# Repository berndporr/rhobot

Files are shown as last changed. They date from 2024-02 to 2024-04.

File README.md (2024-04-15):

# RhoBot: A Robotics and AI platform

RhoBot is a mobile robot for research in obstacle avoidance built using an NVIDIA Jetson Nano, a Slamtec A1M8 RPLiDAR, a Raspberry Pi Cam v2, and two Parallax CR serco motors. The API provided in this repo provides an abstracted way to interface with the motors, however does not currently support interface with the LiDAR or camera so these would need to be implemented by a user.

<p align=center>
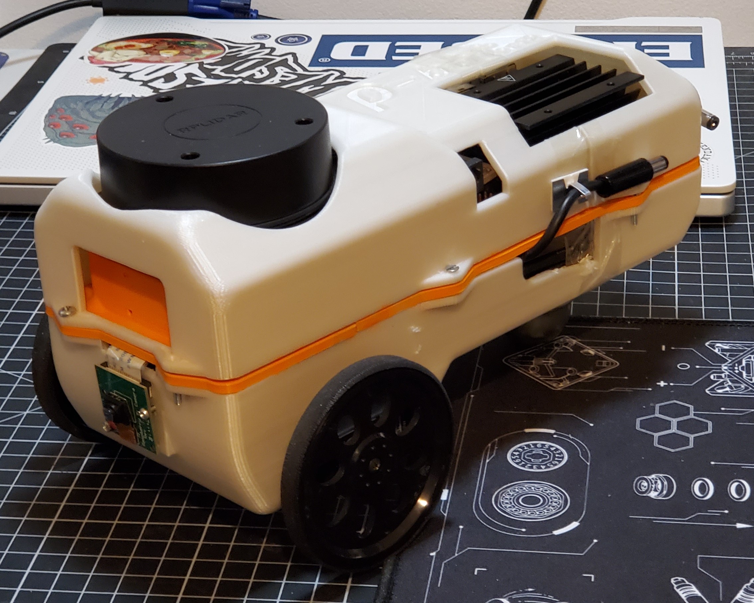
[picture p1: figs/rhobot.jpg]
Rhobot

</p>

## Table of contents

- Bill of Sale
- Enclosure and PCB Manufacture
- Build Guide and Set Up
- API Installation
- Sample Programs
- Credits

## Bill of Sale

| Part | Quantity | Cost (VAT included) | Where to buy |
| --- | --- | --- | --- |
| NVIDIA Jetson Nano | x1 | £167.94 | [RS Components](https://uk.rs-online.com/web/p/processor-development-tools/1999831?gb=s) |
| Parallax CR Servo Motor | x2 | £40.00 | [RS Components](https://uk.rs-online.com/web/p/servo-motors/7813046?gb=s) |
| Parallax Wheels | x2 | £6.40 | [Parallax](https://www.parallax.com/product/robot-wheel-molded-tire-for-servos/) |
| Ansmann Power Supply | x1 | £31.51 | [RS Components](https://uk.rs-online.com/web/p/power-banks/2498449?gb=s) |
| USB-A to DC Jack Cable | x2 | £12.84 | [RS Components](https://uk.rs-online.com/web/p/usb-cables/1862796?gb=s) |
| A1M8 LiDAR | x1 | £83.60 | [RobotShop](https://uk.robotshop.com/products/rplidar-a1m8-360-degree-laser-scanner-development-kit) |
| Raspberry Pi Camera v2 | x2 | £18.61 | [RS Components](https://uk.rs-online.com/web/p/raspberry-pi-cameras/9132664?gb=s) |
| USB Wifi Adapter | x1 | £12.00 | [RS Components](https://uk.rs-online.com/web/p/wifi-adapters/2558455?gb=s) |
| Total | ------- | £372.90 | ------- |

Necessary screws, nuts and bolts are not included in the bill of sale.

## Enclosure and PCB Manufacture

The enclosure is a three teir design and is fully 3D printable. In the CAD directory the their teirs are available in full and split to allow for printing on a smaller printer. The total print time is between 28 - 37 hours depending on material, and around £9 of filament. The weight is 0.3 kg.

If access to a 3D printer is not possible, the service [CraftCloud](craftcloud3d.com) have quoted £23.38 for the manufacture of the enclosure in PLA plastic.

The design files for the PCB were made using KiCAD and are available in the PCB directory. The service [PCBWay](pcbway.com) has quoted £4.01 for the manufacture of 10 boards.

## Build Guide and Set up

### Solder PCB
Firstly, sockets should be soldered onto the custom PCB. The 40 pin socket should be soldered to the bottom of the board and the remaining sockets should be mounted to the top of the board.

<p align=center>
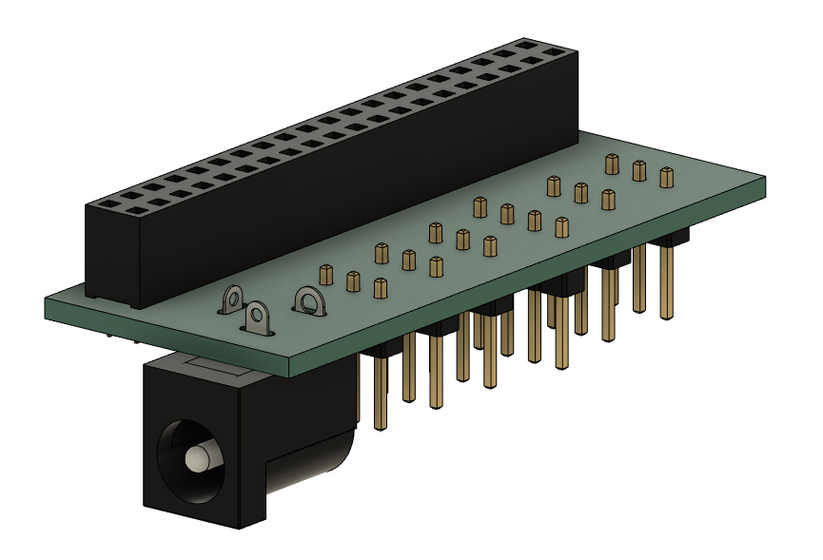
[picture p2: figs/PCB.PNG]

</p>

### Lowest Level
1) Screw the wheels onto the motors.
2) Use nuts and bolts to attach both motors to the "lower" enclosure component in the four mounting holes. Ensure the cables of the motors point towards the front of the enclosure so they will line up with the center of the LiDAR.
3) Use bolts screws to attach the camera to the mount on the "lower" component and route it's cable to the back of the enclosure.
4) Rest the power supply on top of the motors with the ports facing the back of the enclosure. Connect the USB-A to DC cables to the USB ports of the supply.

<p align=center>
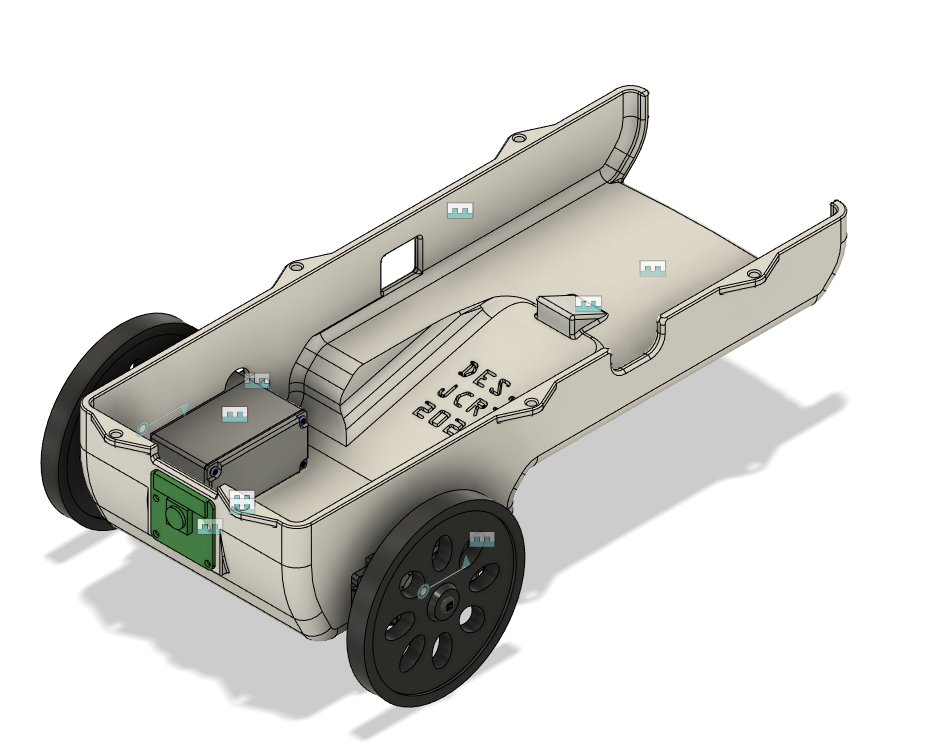
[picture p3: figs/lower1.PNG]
Lower A
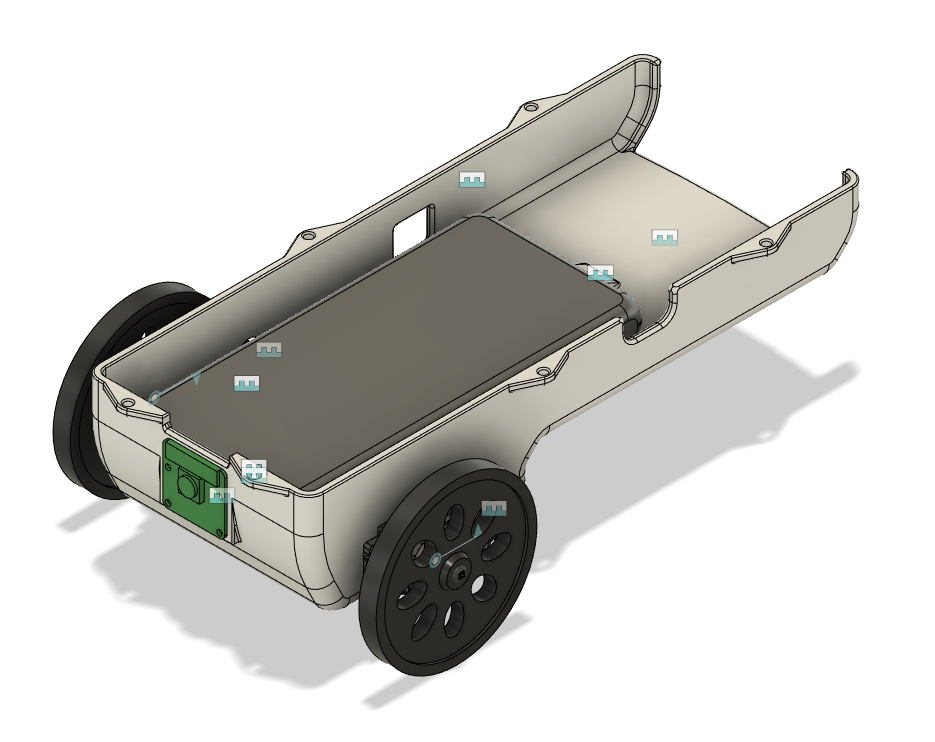
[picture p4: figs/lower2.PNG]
Lower B
 
</p>

### Middle Level
1) Use bolts to secure the Jetson to the lower standoffs of the "middle" enclosure component.
2) Use boolts to secure the LiDAR sensor to the higher standoffs of the "middle" component.
3) Attach the PCB to the 40 pin GPIO header of the Jetson.
4) Route the motors and camera wire through the slots in the "middle" component. Attach the camera cable to the CSI port of the Jetson. Attach the motors to the PCB using the relevant sockets, noting the circuit schematic.
5) Connect the LiDAR UART and motor cables to the PCB noting the schematic.
6) Place the "middle" component over the "lower" component.

<p align=center>
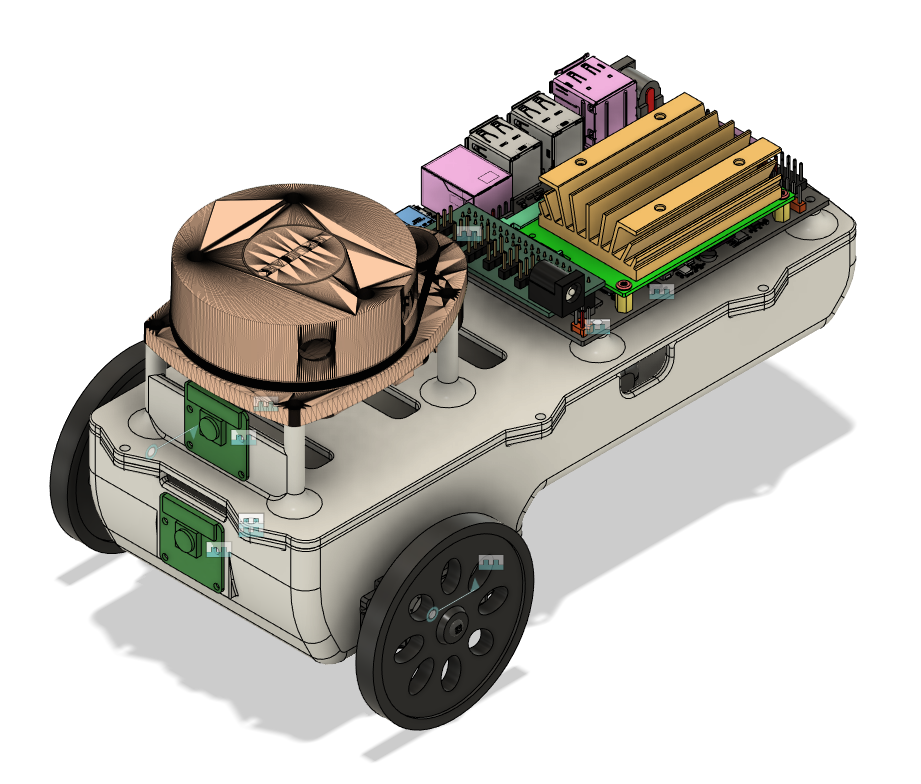
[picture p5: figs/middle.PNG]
Middle

</p>

### Upper Level
1) Place the "upper" component onto the "middle" componet and secure the enclosure with the sixe bolt holes around the perimeter.
2) Attach the USB Wifi adapter to a USB port on the Jetson
3) Connect the power supply to the Jetson and PCB through using the USB to DC cables.

<p align=center>
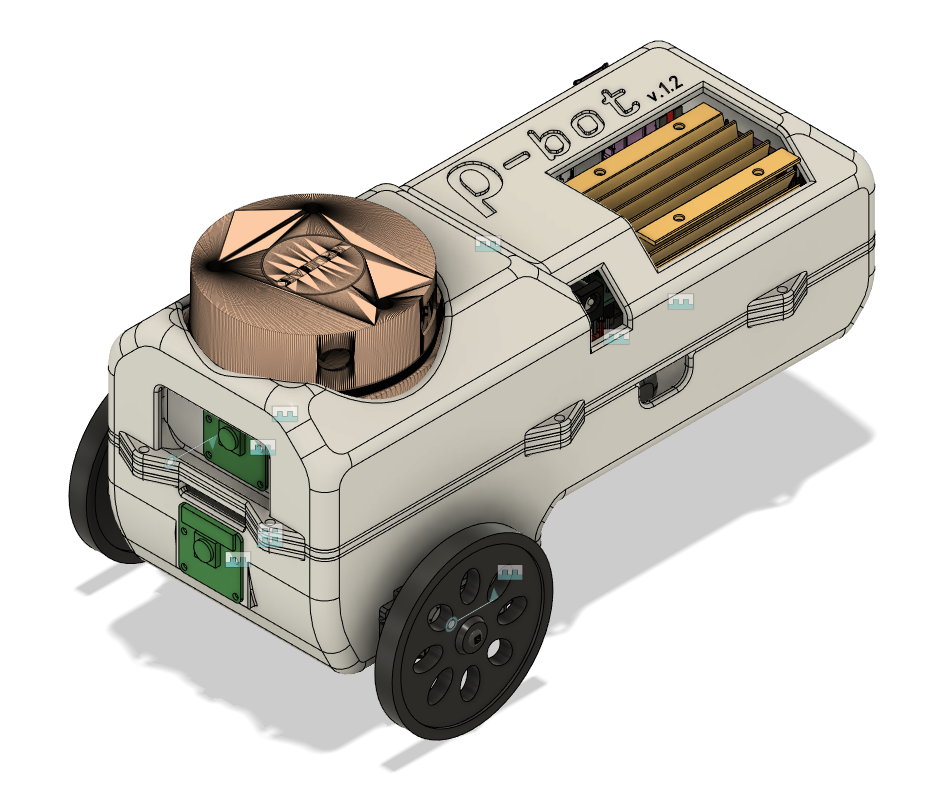
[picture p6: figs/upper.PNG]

</p>

### Jetson Set Up
For detailed instructions how how to set up the Jetson, click this [link](https://developer.nvidia.com/embedded/learn/get-started-jetson-nano-devkit).

Once the Jetson boots, connect to a wireless network using the Linux network manager.

## API Installation

### Dependencies
Clone and build the [JetsonGPIO](https://github.com/pjueon/JetsonGPIO) repository. This will install the library used to interface with the Jetson's GPIO header.

For the camer and LiDAR, the [jetson-inference]()https://github.com/dusty-nv/jetson-inference and [rplidar-sdk](https://github.com/Slamtec/rplidar_sdk) are recommended respectively.

### Build Project
Clone this repository and run the following commands to build the project:

`mkdir build && cd build`

`cmake ..`

`make`

This will build the API library and compile the sample programs.

## Sample Programs

sample programs are provided to test the motor interface. To execute them run the relevant of the following commands while in the build directory:

`./test_motors`

`./test_differential_steering`

`./test_lidar`

## Credits

This project has been supervised by Dr. Bernd Porr and is a continuation of work done on the [AlphaBot](https://github.com/berndporr/alphabot) and [SigmaBot](https://github.com/berndporr/sigmabot) projects.

RhoBot is ©️ copyright 2024 of J.C. Redmond III and any use of the material in this repository should be appropriately credited.

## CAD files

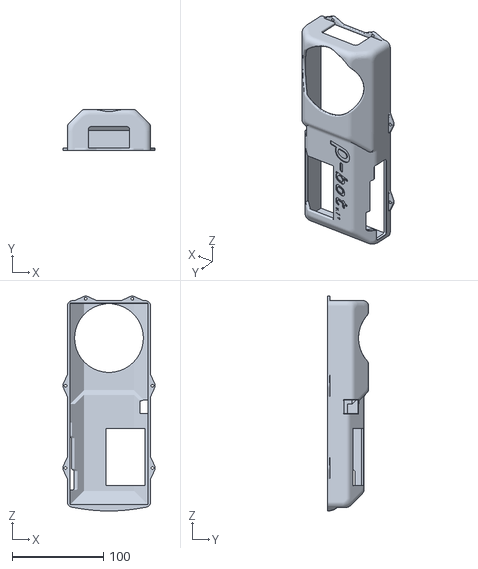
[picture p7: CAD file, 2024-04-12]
CAD/upper_full.stl
101.0 x 45.0 x 235.0

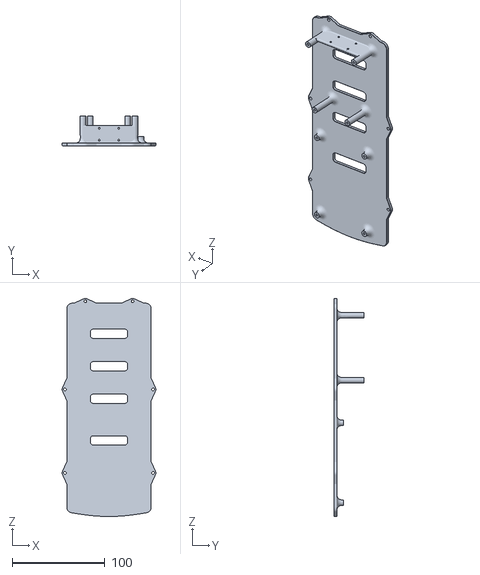
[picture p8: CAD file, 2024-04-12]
CAD/middle_full.stl
101.0 x 32.0 x 235.0

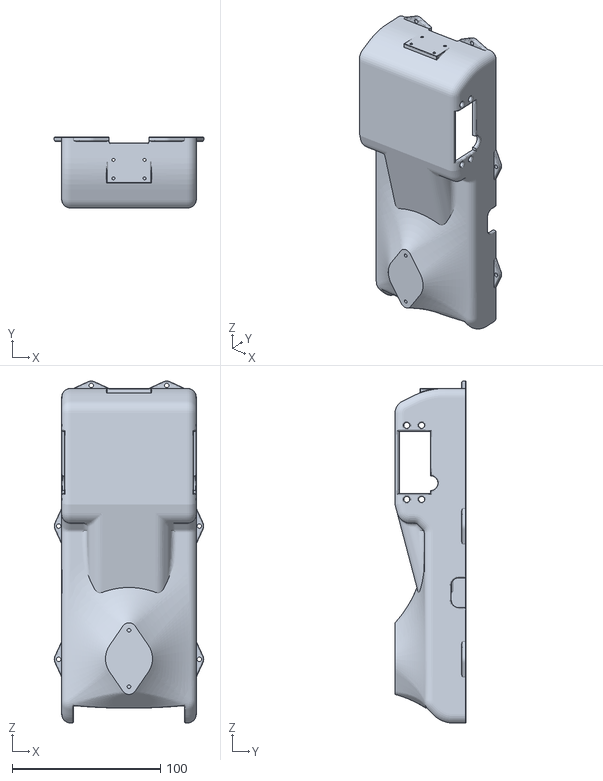
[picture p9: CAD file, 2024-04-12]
CAD/lower_full.stl
101.0 x 48.0 x 231.0

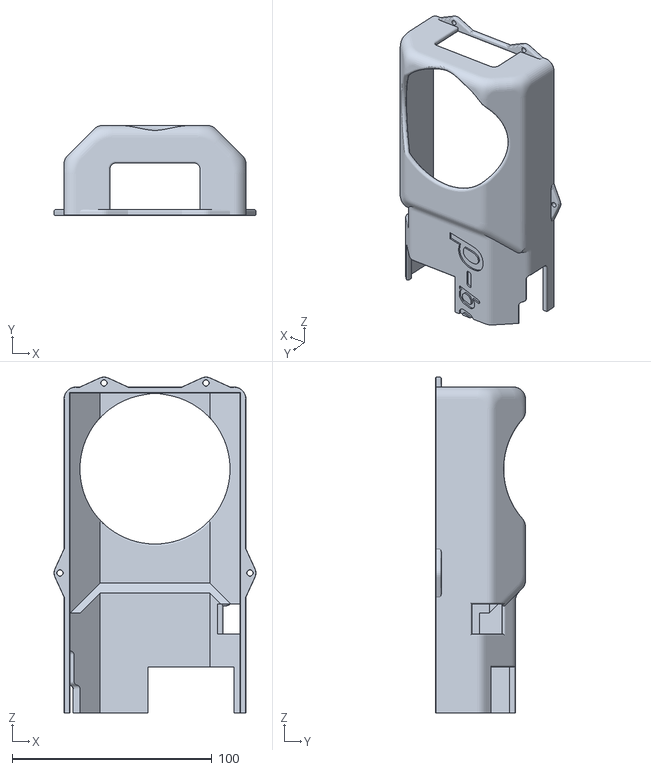
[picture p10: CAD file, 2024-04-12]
CAD/split components/upper_A.stl
101.0 x 45.0 x 168.0

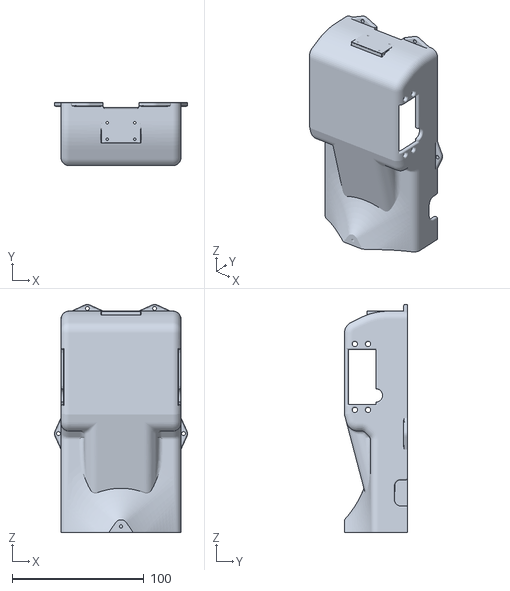
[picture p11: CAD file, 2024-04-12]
CAD/split components/lower_A.stl
101.0 x 48.0 x 173.0

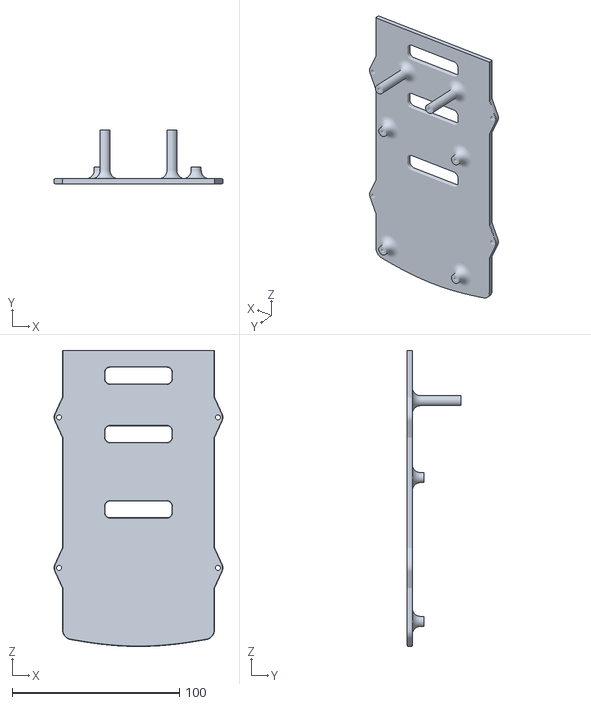
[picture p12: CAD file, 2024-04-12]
CAD/split components/middle_B.stl
101.0 x 32.0 x 177.0

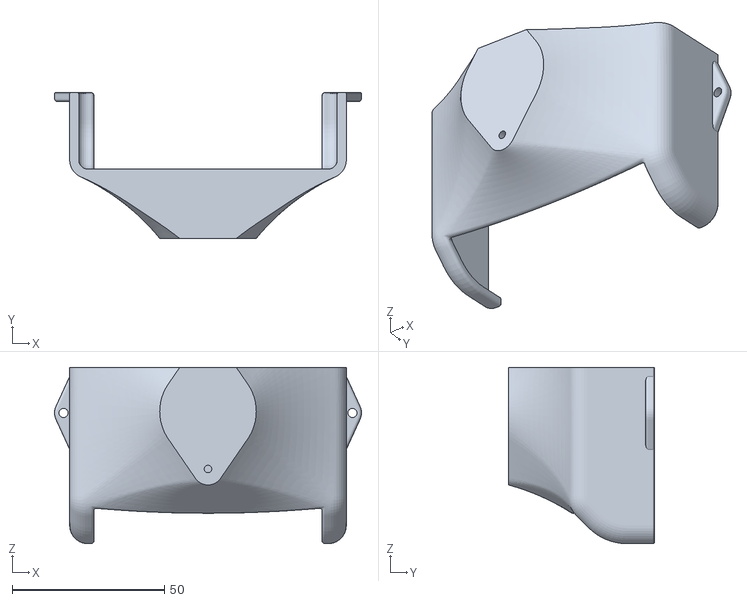
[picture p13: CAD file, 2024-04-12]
CAD/split components/lower_B.stl
101.0 x 48.0 x 58.0

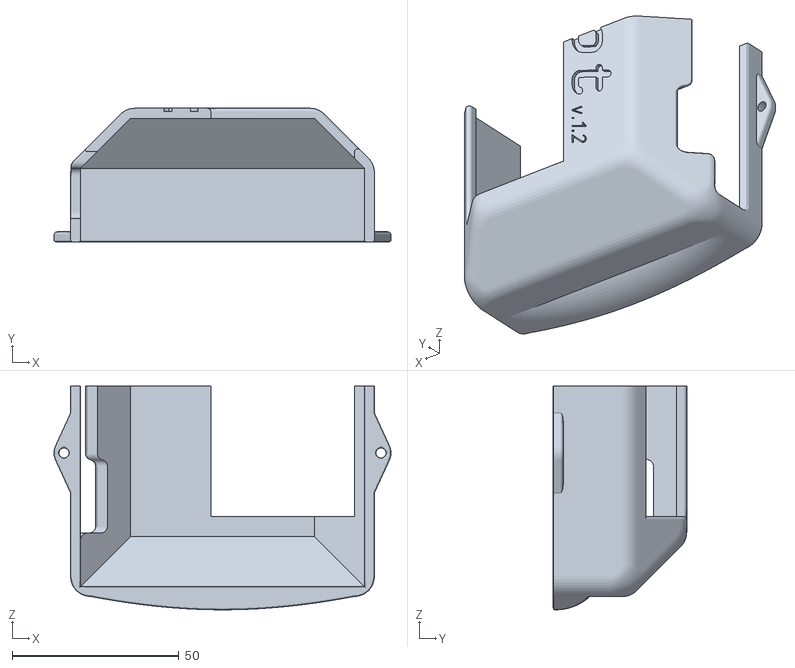
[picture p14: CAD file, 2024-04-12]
CAD/split components/upper_B.stl
101.0 x 40.0 x 67.0

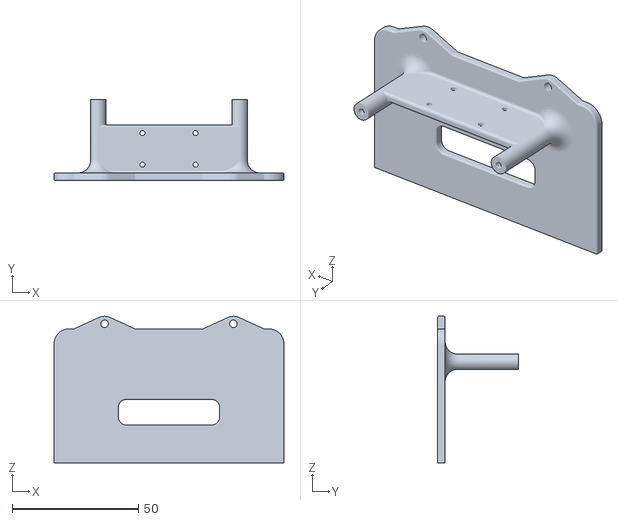
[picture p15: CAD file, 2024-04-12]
CAD/split components/middle_A.stl
91.0 x 32.0 x 58.0

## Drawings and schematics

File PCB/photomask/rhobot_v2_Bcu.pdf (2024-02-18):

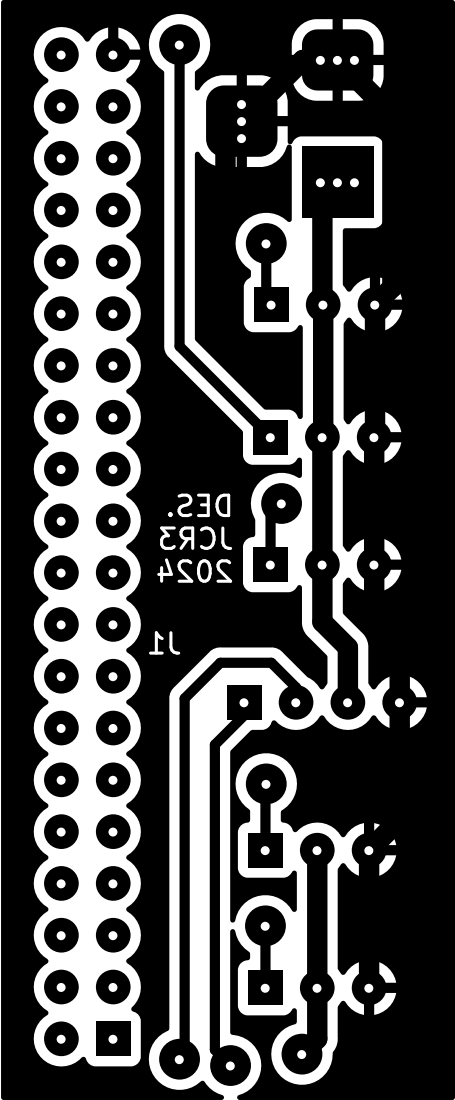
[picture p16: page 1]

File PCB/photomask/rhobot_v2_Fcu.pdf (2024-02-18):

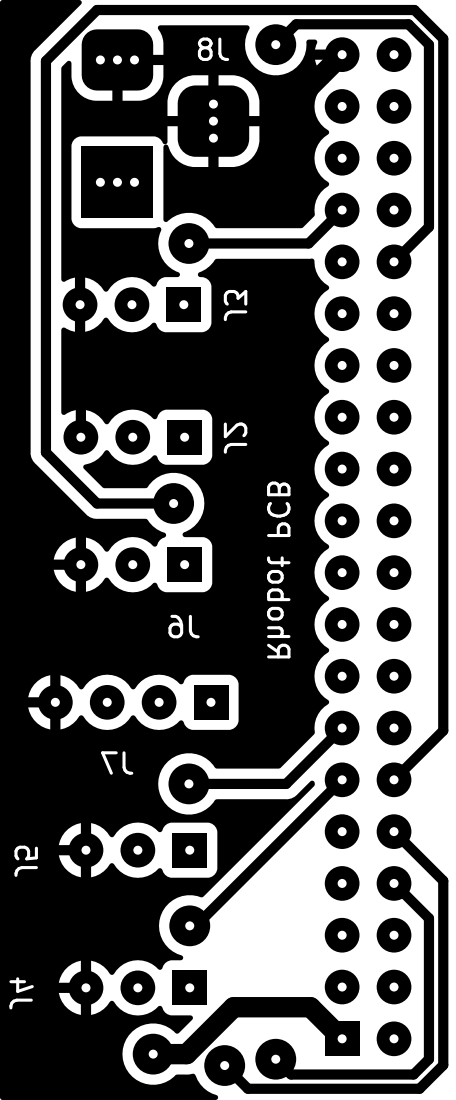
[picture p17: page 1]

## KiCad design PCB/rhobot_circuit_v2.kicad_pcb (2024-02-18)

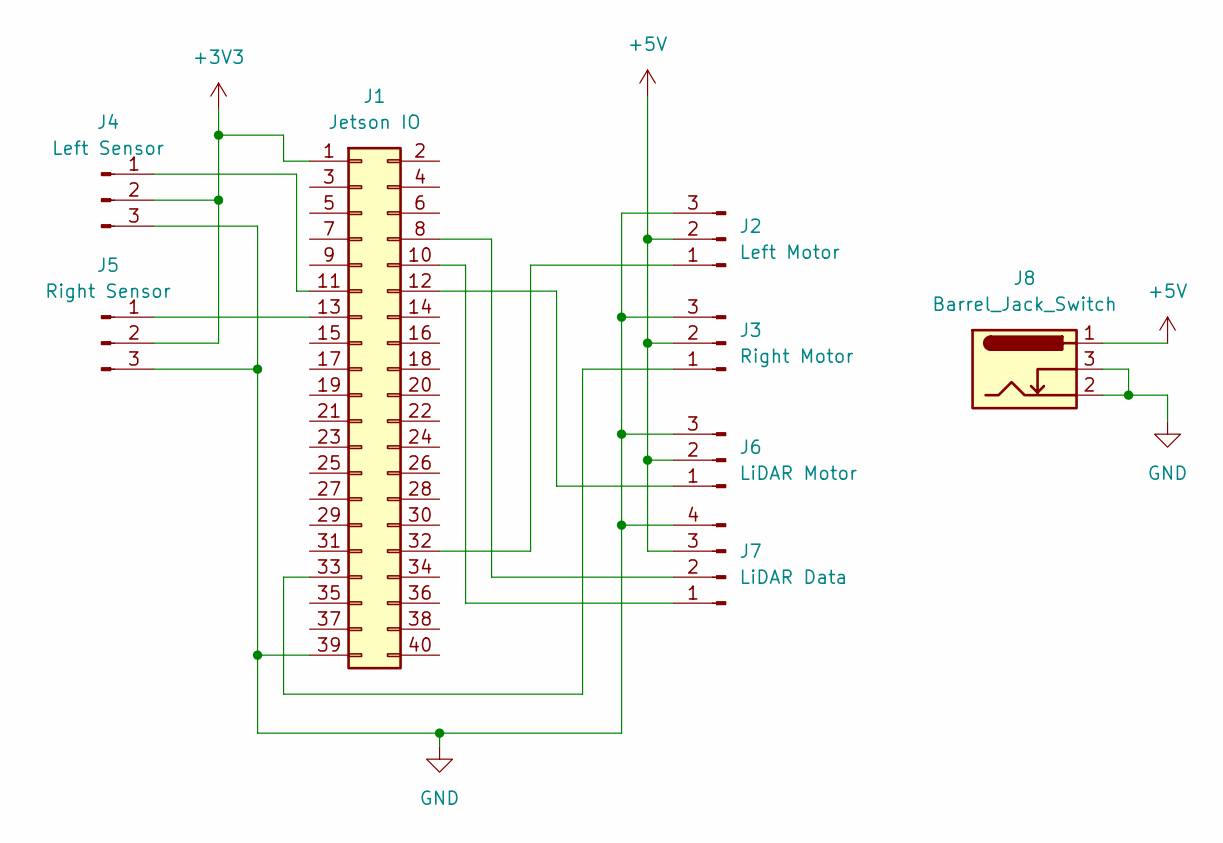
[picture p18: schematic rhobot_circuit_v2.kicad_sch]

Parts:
J1: Jetson IO; PinSocket_2x20_P2.54mm_Vertical
J2: Left Motor; PinHeader_1x03_P2.54mm_Vertical
J3: Right Motor; PinHeader_1x03_P2.54mm_Vertical
J4: Left Sensor; PinHeader_1x03_P2.54mm_Vertical
J5: Right Sensor; PinHeader_1x03_P2.54mm_Vertical
J6: LiDAR Motor; PinHeader_1x03_P2.54mm_Vertical
J7: LiDAR Data; PinHeader_1x04_P2.54mm_Vertical
J8: Barrel_Jack_Switch; BarrelJack_Horizontal

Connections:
+3V3: J1.1, J4.2, J5.2
+5V: J2.2, J3.2, J6.2, J7.3, J8.1
GND: J1.39, J2.3, J3.3, J4.3, J5.3, J6.3, J7.4, J8.2, J8.3
unnamed: J1.8, J7.2
unnamed: J1.10, J7.1
unnamed: J1.11, J4.1
unnamed: J1.12, J6.1
unnamed: J1.13, J5.1
unnamed: J1.32, J2.1
unnamed: J1.33, J3.1

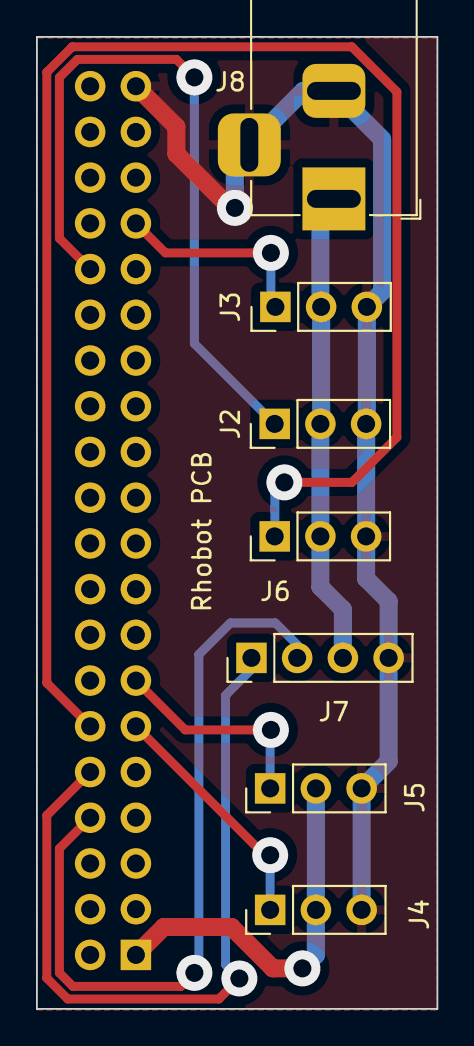
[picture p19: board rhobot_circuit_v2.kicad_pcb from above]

Board: 2 copper layers, 22.2 x 54.0 mm, 8 parts (1 on the bottom side), 10 nets.

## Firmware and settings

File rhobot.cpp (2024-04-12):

#include "rhobot.h"

#include <chrono>
#include <map>
#include <string>

float RhoBot::getDutyCycleFromSpeed(float speed) {
    // take in speed from -1 to 1 (backwards to forwards) and return the calibrated pwm for the motors
    // motor datasheet requests an on time of 1.5 ms for stationary, 1.7 ms for max anticlockwise and 1.3 for max clockwise
    
    // map speed from -1 -> 1 to 0.0013 -> 0.0017
    // first goes from -1 -> 1 to 0 -> 1, then 0 -> 0.004 and finally 0.0013 -> 0.0017
    float onTime = ( (speed + 1.0) / 2.0 ) * 0.0004 + 0.0013;

    float period = 1.0 / pwmFrequency;
    float dutyCycle = onTime / period * 100.0;
    
    return dutyCycle;
}

void RhoBot::initPWM() {

    // create the pwm objects and reset the pointers to point at them
    GPIO::setup(GPIO_MOTORL, GPIO::OUT, GPIO::HIGH);
    std::unique_ptr<GPIO::PWM> pwmLeft = std::make_unique<GPIO::PWM>(GPIO::PWM(GPIO_MOTORL, 50));
    pwmLeftPointer = std::move(pwmLeft);

    GPIO::setup(GPIO_MOTORR, GPIO::OUT, GPIO::HIGH);
    std::unique_ptr<GPIO::PWM> pwmRight = std::make_unique<GPIO::PWM>(GPIO::PWM(GPIO_MOTORR, 50));
    pwmRightPointer = std::move(pwmRight);

    // set frequency of the pwms
    pwmLeftPointer->ChangeFrequency(pwmFrequency);
    pwmRightPointer->ChangeFrequency(pwmFrequency);

    pwmLeftPointer->start(getDutyCycleFromSpeed(0.0));
    pwmRightPointer->start(getDutyCycleFromSpeed(0.0));

}

void RhoBot::initSoftPWM() {

    // pin set up as gpio out
    GPIO::setup(GPIO_LiDARMOTOR, GPIO::OUT, GPIO::LOW);

    // set pin control function to run in antoher thread
    softPwmWorker = std::thread(&RhoBot::softPwmPinControl, this);

}

void RhoBot::start() {

    // this variable is used to ensure methods only execute after start has been called and things have been set up
    running = true;

    GPIO::setmode(GPIO::BOARD);
    GPIO::setwarnings(false);
    initPWM();
    initSoftPWM();
}

void RhoBot::stop() {

    if (!running) return;

    setLeftWheelSpeed(0.0);
    setRightWheelSpeed(0.0);
    setLiDarMotorSpeed(0.0);
    
    running = false;

    // join this worker back
    softPwmWorker.join();

    // stop the pwm and clean up gpio
    GPIO::output(GPIO_LiDARMOTOR, GPIO::LOW);
    pwmLeftPointer->stop();
    pwmRightPointer->stop();
    GPIO::cleanup();
}

void RhoBot::setLeftWheelSpeed(float speed) {

    if (!running) return;

    // make sure speed is in the right bounds
    if (speed < -1)
            speed = -1;
    if (speed > 1)
            speed = 1;
    
    leftWheelSpeed = speed;
    pwmLeftPointer->ChangeDutyCycle(getDutyCycleFromSpeed(speed));

}

void RhoBot::setRightWheelSpeed(float speed) {

    if (!running) return;

    // make sure speed is in the right bounds
    if (speed < -1)
            speed = -1;
    if (speed > 1)
            speed = 1;
    
    // minus speed so +1 is forward for both motors
    leftWheelSpeed = -speed;
    pwmRightPointer->ChangeDutyCycle(getDutyCycleFromSpeed(-speed));
}


void RhoBot::moveInline(float distInMeters, bool forward) {

    if (!running) return;

    // rough estimation of open loop dynamics to move inline a distance in meters
    // this will be improved by the addition of speed sensors on both wheels to provide feedback

    float onTimeInSeconds = distInMeters * 360.0 / (2 * 3.1415 * r_wheel * wheel_speed);
    
    float speed = 1.0;
    if (!forward) {speed = -speed;}

    setLeftWheelSpeed(speed);
    setRightWheelSpeed(speed);

    std::this_thread::sleep_for(std::chrono::duration<double>(onTimeInSeconds));

    setLeftWheelSpeed(0.0);
    setRightWheelSpeed(0.0);

}

void RhoBot::changeHeading(float angleInDegrees, bool clockwise) {

    if (!running) return;

    // rough estimation of open loop dynamics to move inline a distance in meters
    // this will be improved by the addition of speed sensors on both wheels to provide feedback

    float onTimeInSeconds = angleInDegrees * (2 * r_turn) / (r_wheel * wheel_speed);
    
    float speed = 1.0;
    if (!clockwise) {speed = -speed;}

    setLeftWheelSpeed(speed);
    setRightWheelSpeed(-speed);

    std::this_thread::sleep_for(std::chrono::duration<double>(onTimeInSeconds));

    setLeftWheelSpeed(0.0);
    setRightWheelSpeed(0.0);

}

void RhoBot::setLiDarMotorSpeed(float speed) {

    if (!running) return;

    // make sure speed is in the right bounds
    if (speed < 0.0)
            speed = 0.0;
    if (speed > 1.0)
            speed = 1.0;

    // this is effectively the duty cycle
    lidarMotorSpeed = speed;

    // calculate the on time here so don't have to repeat the computation
    lidarMotorOnTime = lidarMotorSpeed * (1.0 / (float)softPwmFrequency); // in seconds

    // calculate the on time here so don't have to repeat the computation
    lidarMotorOffTime = (1.0 - lidarMotorSpeed) * (1.0 / (float)softPwmFrequency); // in seconds

}

void RhoBot::softPwmPinControl() {

    while (running) { // from start called to stop called

        if (lidarMotorSpeed < 0.1){ // dont turn pin on if speed is tiny
            GPIO::output(GPIO_LiDARMOTOR, GPIO::LOW);
        }
        else if (lidarMotorSpeed > 0.9){ // dont turn pin off if speed is big
            GPIO::output(GPIO_LiDARMOTOR, GPIO::HIGH);
        }
        else {
            
            // turn high, sleep for on time and turn low
            GPIO::output(GPIO_LiDARMOTOR, GPIO::HIGH);
            std::this_thread::sleep_for(std::chrono::duration<double>(lidarMotorOnTime)); // on time

            GPIO::output(GPIO_LiDARMOTOR, GPIO::LOW);
            std::this_thread::sleep_for(std::chrono::duration<double>(lidarMotorOffTime)); // off time

        }

    }

}

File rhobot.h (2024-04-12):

#ifndef RHOBOT_H
#define RHOBOT_H

#include <vector>
#include <thread>
#include <JetsonGPIO.h>

// Rhoabot class for hardware communication (API)

class RhoBot
{

    public:

        // Starts the communication with the robot.
        void start();

        // Stops the communication with the Alphabot
        void stop();

        // Deconstructor
        ~RhoBot()
        {
            stop();
        }

        // Set the left wheel speed between -1 and +1
        void setLeftWheelSpeed(float speed);

        // Set the right wheel speed between -1 and +1
        void setRightWheelSpeed(float speed);

        // Move forward or backward a certain number of meters
        void moveInline(float distInMeters, bool forward);

        // Turn left or right by a certain number of degrees
        void changeHeading(float angleInDegrees, bool clockwise);

        // set LiDAR motor speed between 0 and 1
        void setLiDarMotorSpeed(float speed);

        // Get LiDAR data

        // Get camera data

    private:

        // Motor pins
        // note that these are BOARD numbering scheme
        static const int GPIO_MOTORL = 32;
        static const int GPIO_MOTORR = 33;
        static const int GPIO_LiDARMOTOR = 12;

        // Pointers to PWM objects
        std::unique_ptr<GPIO::PWM> pwmLeftPointer;
        std::unique_ptr<GPIO::PWM> pwmRightPointer;
        
        // PWM parameters
        static constexpr float pwmFrequency = 60.0; // Hz
        float leftWheelSpeed = 0.0; // -1.0 to 1.0
        float rightWheelSpeed = 0.0; // -1.0 to 1.0

        // soft PWM paramteres
        static const int softPwmFrequency = 40; // Hz
        float lidarMotorSpeed = 0.0; // 0 to 1.0
        float lidarMotorOnTime = 0.0;
        float lidarMotorOffTime = 0.0;
        std::thread softPwmWorker;

        // Physcial measurements for open loop dynamics in meters and degrees
        float r_wheel = 0.065;
        float r_turn = 0.06;
        // Max angular speed of wheel in degrees/s
        float wheel_speed = 150;

        bool running = false;

        // Find the necessary duty cyle for motors based on the speed (-1 to +1)
        float getDutyCycleFromSpeed(float speed);

        // Initialise both hardware pwm pins
        void initPWM();

        // Set up the software PWM
        void initSoftPWM();

        // Do the actual pin control for the soft PWM on another thread
        void softPwmPinControl();

};

#endif

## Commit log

2024-01-25 simple calibrated motor test
2024-03-12 pwm working on pcb
2024-03-13 motor test
2024-03-14 API wokring for motor control
2024-03-14 motor test code
2024-03-15 differential steering working
2024-03-15 updated steering test
2024-03-29 soft pwm control
2024-04-04 tested camera
2024-04-10 soft pwm optimisation
2024-04-10 off time for soft pwm!
2024-04-12 working soft pwm
2024-04-12 soft pwm freq
2024-04-12 Updated CAD
    [lower_A.stl, lower_B.stl, lower_full.stl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]
